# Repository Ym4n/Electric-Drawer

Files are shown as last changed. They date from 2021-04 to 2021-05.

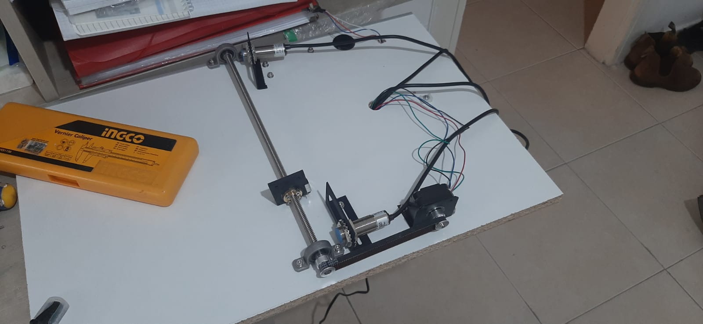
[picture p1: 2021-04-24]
pic & video/Assembly.jpeg

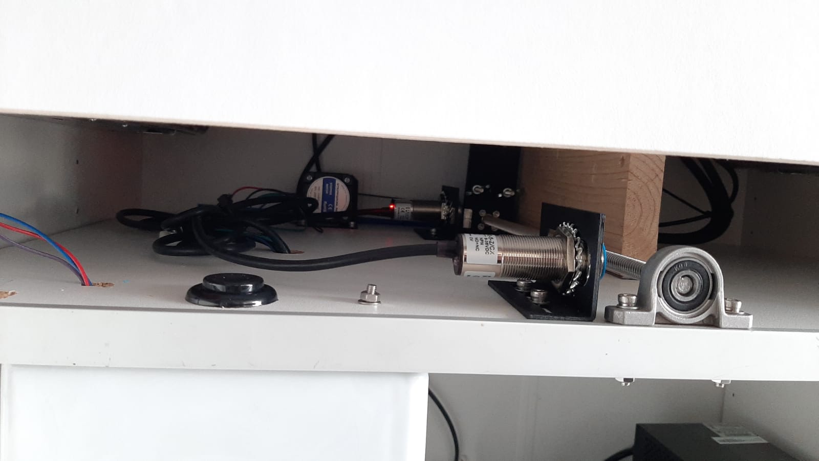
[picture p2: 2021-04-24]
pic & video/Final result.jpeg

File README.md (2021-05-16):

# Electric-Drawer
Electric Drawer for laser projector. control by Arduino.

https://user-images.githubusercontent.com/82320340/115971307-6bd4b180-a550-11eb-89f3-70404eacda08.mp4

# The Goal -
1.  Drawer can pool in and out to a specific position - No more manual operation.
2. Accuracy position - No more fine tune the projector to the accurate projection position. 
With every 1mm of distance between projector’s back to the projection surface, 0.2 inches are gained in picture size. 
see video below -

https://user-images.githubusercontent.com/82320340/115971346-9a528c80-a550-11eb-801a-cefcc77d8984.mp4

# How Dose it work?
1. User sends command with a remote control to IR reader or click on an arcade button . 
(Note: currently I aded 2 remotes. You can add/remove/change it)
2. IR-reader/button signal connected to Arduino.
3. Arduino decides to which position to get to. Far out or far in. 
In case of the drawer is already in the correct position, no movement will be made. 
(This is being determined by the Arduino using the two sensors that are located at the beginning and end of the movement range).
4. Motion control by arduino ,stepper motor and inductive sensors.

you can check mechanical design at solidworks folder or electrical design in electrical drawing .

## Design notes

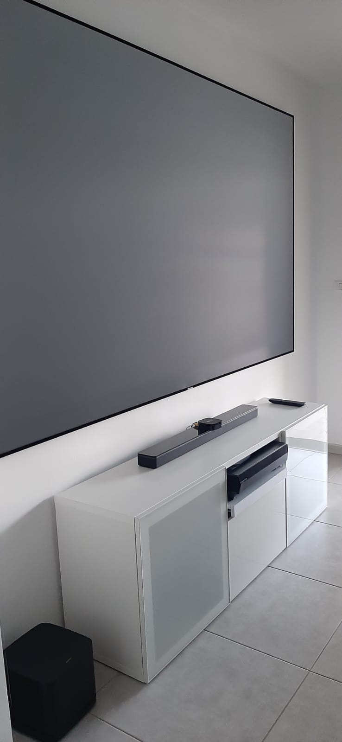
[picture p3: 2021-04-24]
pic & video/top view.jpeg

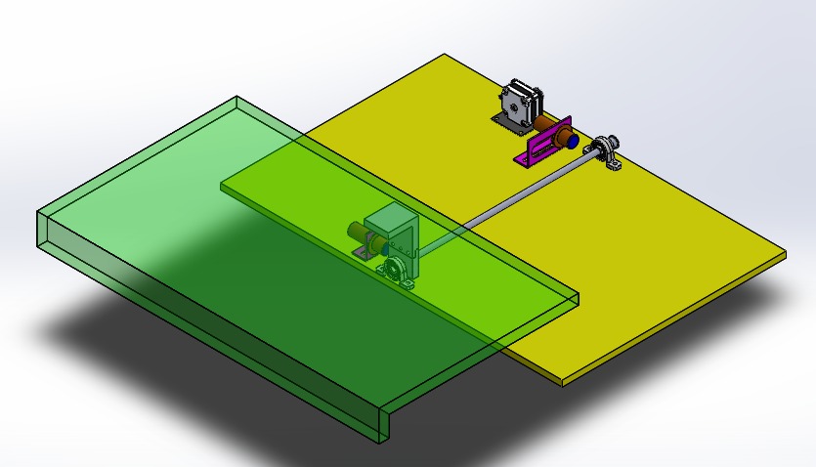
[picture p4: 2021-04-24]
pic & video/Solidworks.jpeg

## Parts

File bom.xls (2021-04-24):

ITEM NO. | PART NAME | QTY. | supplier
1 | bearing KP08 | 2 | Aliexpress
2 | lead screw Lead-8mm Len-350mm | 1 | Aliexpress
3 | Short Body Nema 17 17HS08-1004S | 1 | Aliexpress
4 | Inductive sensor | 2 | Aliexpress
5 | Pulley 8mm | 1 | Aliexpress
6 | Pulley 5mm | 1 | Aliexpress
7 | T8 nut | 1 | Aliexpress
8 | Arcade Button | 1 | Aliexpress
9 | Terminal block | 1 | Aliexpress
10 | electronics box 150x190 | 1 | Electronic store
11 | Arduino uno | 1 | Electronic store
12 | l298n motor driver | 1 | Electronic store
13 | Infra red remote control kit | 1 | Electronic store
14 | power supply 12v 2A | 1 | Electronic store
15 | Mount Inductive sensor | 2 | 3D printing
16 | MotorMount_NEMA | 1 | 3D printing
17 | finger down | 1 | 3D printing
18 | finger up | 1 | 3D printing
19 | plate | 1 | Recycled wood
20 | drawer | 1 | Recycled wood
21 | cabinet base | 1 | -

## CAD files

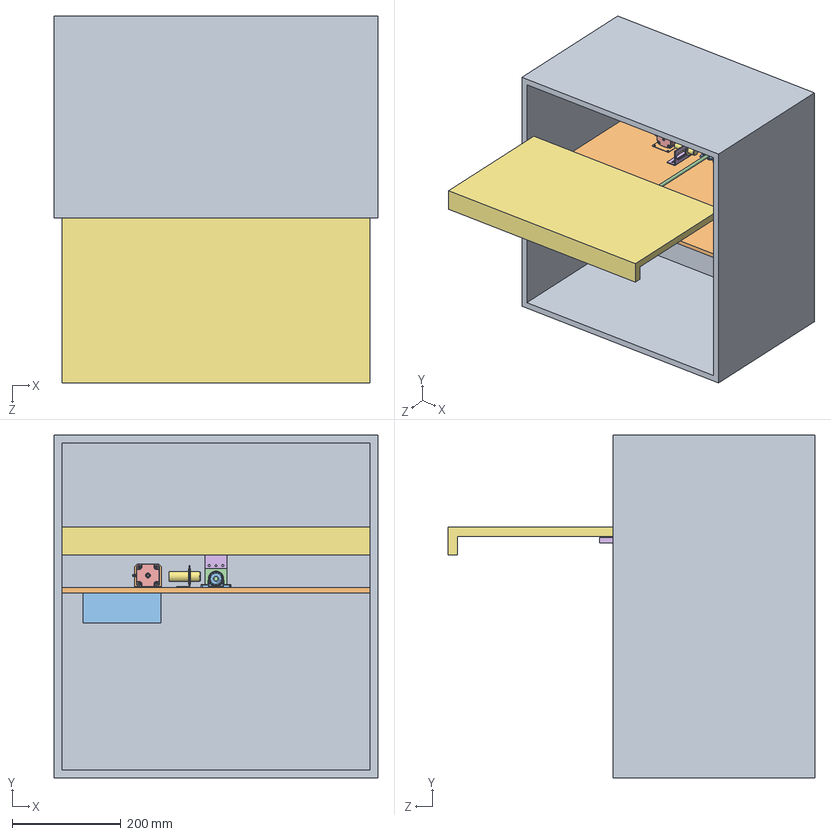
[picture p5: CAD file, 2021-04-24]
solidworks/main.SLDASM
595.0 x 630.0 x 674.0 mm
plate
bearing KP08 x 2
lead screw Lead-8mm Len-350mm
17HS08-1004S
slot Inductive sensor x 2
Inductive sensor x 2
Pulley 8mm
Pulley 5mm
MotorMount_NEMA
electronics box 150x190
finger down
T8 nut
finger up
drawer

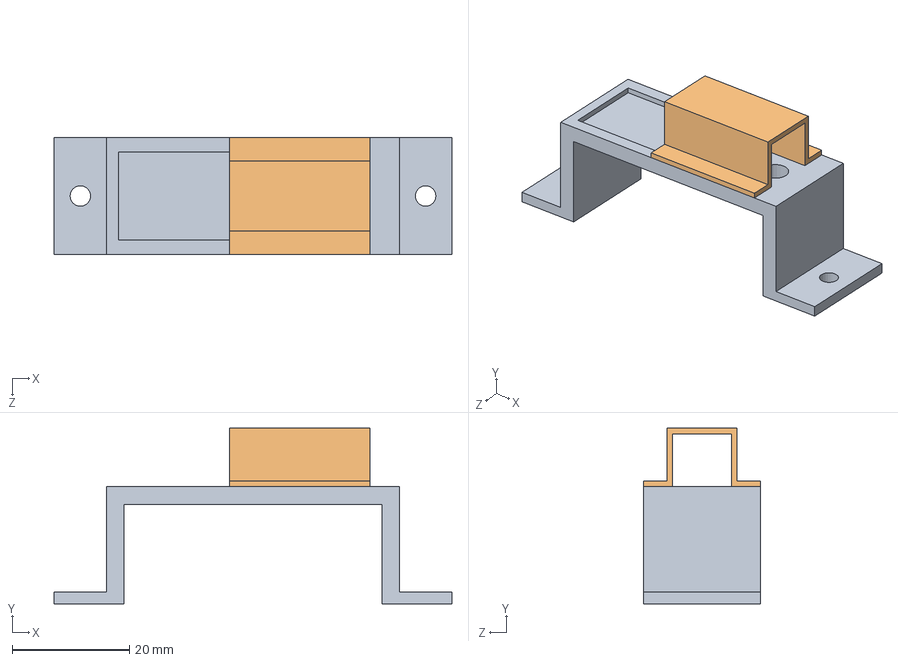
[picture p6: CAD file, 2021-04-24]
solidworks/remote base.SLDASM
68.0 x 30.0 x 20.0 mm
remote sensor house
remote sensor house2

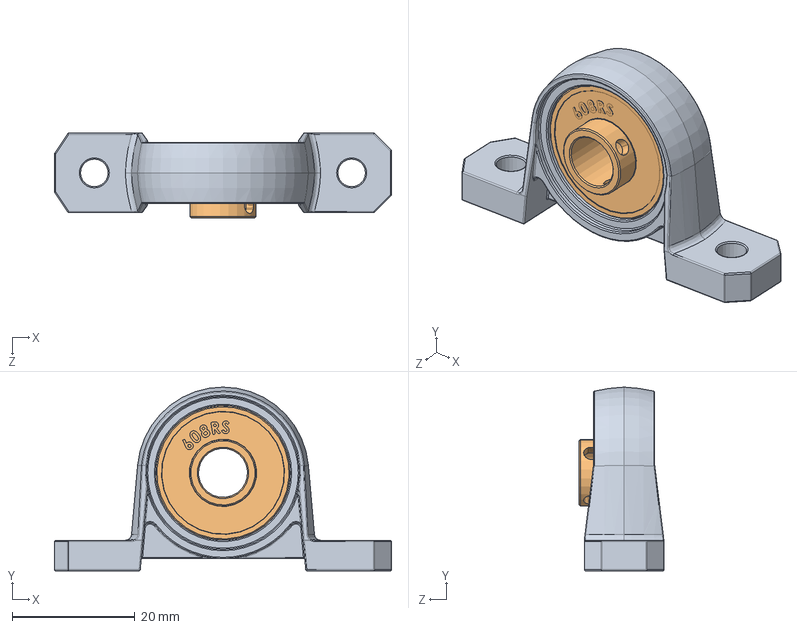
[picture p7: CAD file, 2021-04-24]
solidworks/KP08.SLDASM
55.0 x 30.0 x 13.9 mm
KP08
608RS

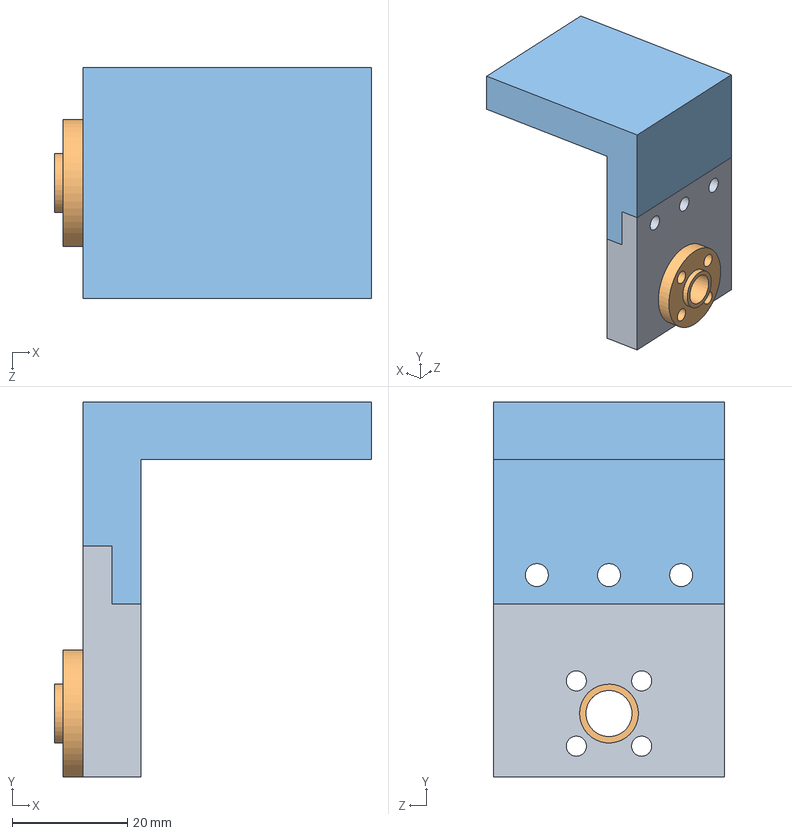
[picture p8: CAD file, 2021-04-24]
solidworks/moving part.SLDASM
55.0 x 65.0 x 40.0 mm
finger down
T8 nut
finger up

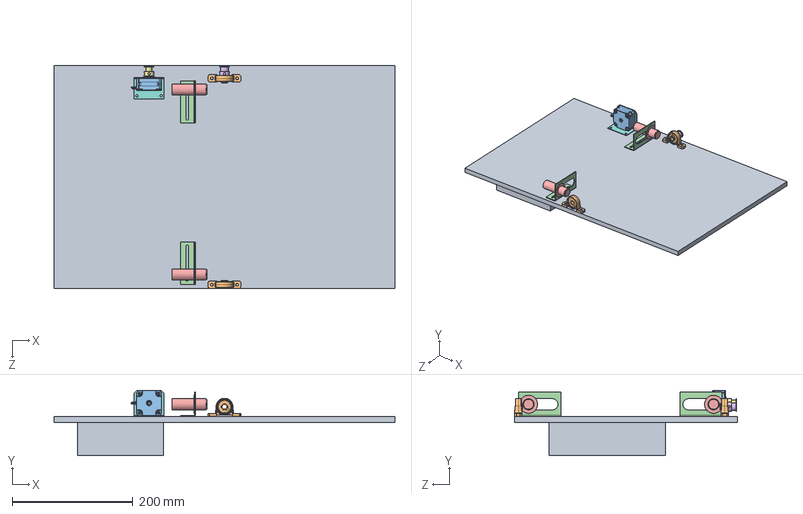
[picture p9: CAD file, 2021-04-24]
solidworks/sum-main motion control assembly.SLDASM
565.0 x 108.0 x 370.0 mm
plate
bearing KP08 x 2
17HS08-1004S
slot Inductive sensor x 2
Inductive sensor x 2
Pulley 8mm
Pulley 5mm
MotorMount_NEMA
electronics box 150x190

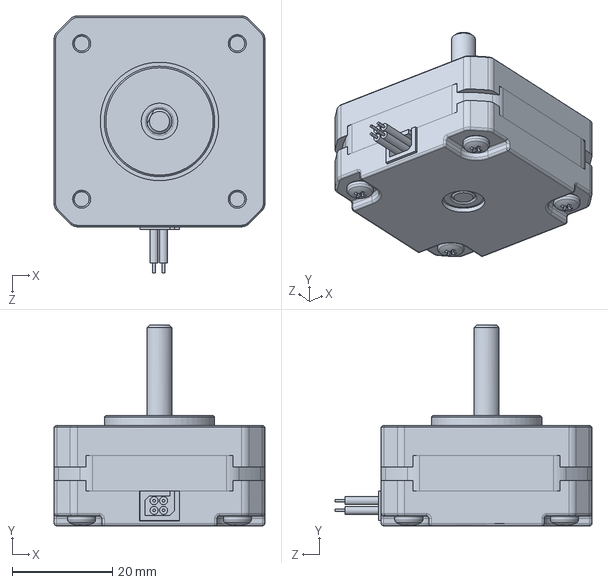
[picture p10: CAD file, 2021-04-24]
solidworks/Short Body Nema 17 17HS08-1004S.SLDPRT
42.0 x 40.0 x 51.2 mm

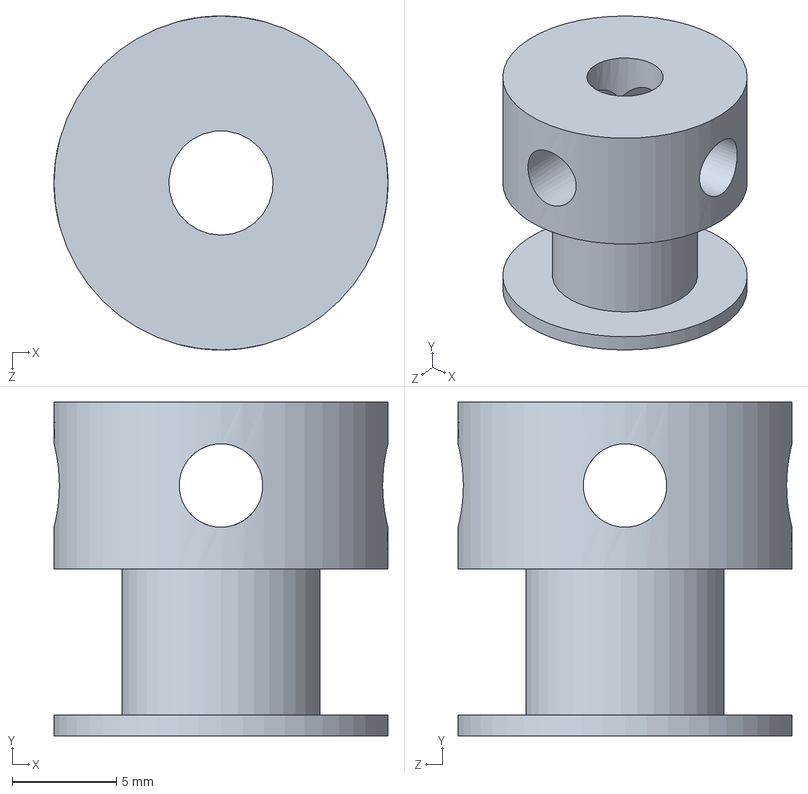
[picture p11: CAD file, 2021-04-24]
solidworks/Pulley 5mm.SLDPRT
16.0 x 16.0 x 16.0 mm

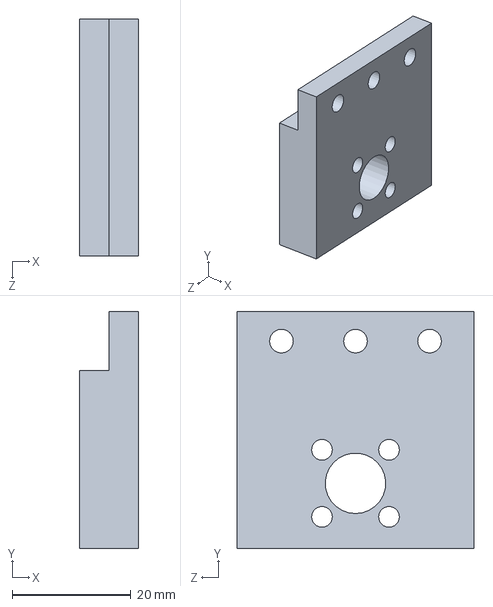
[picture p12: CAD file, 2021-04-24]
solidworks/finger down.SLDPRT
10.0 x 40.0 x 40.0 mm

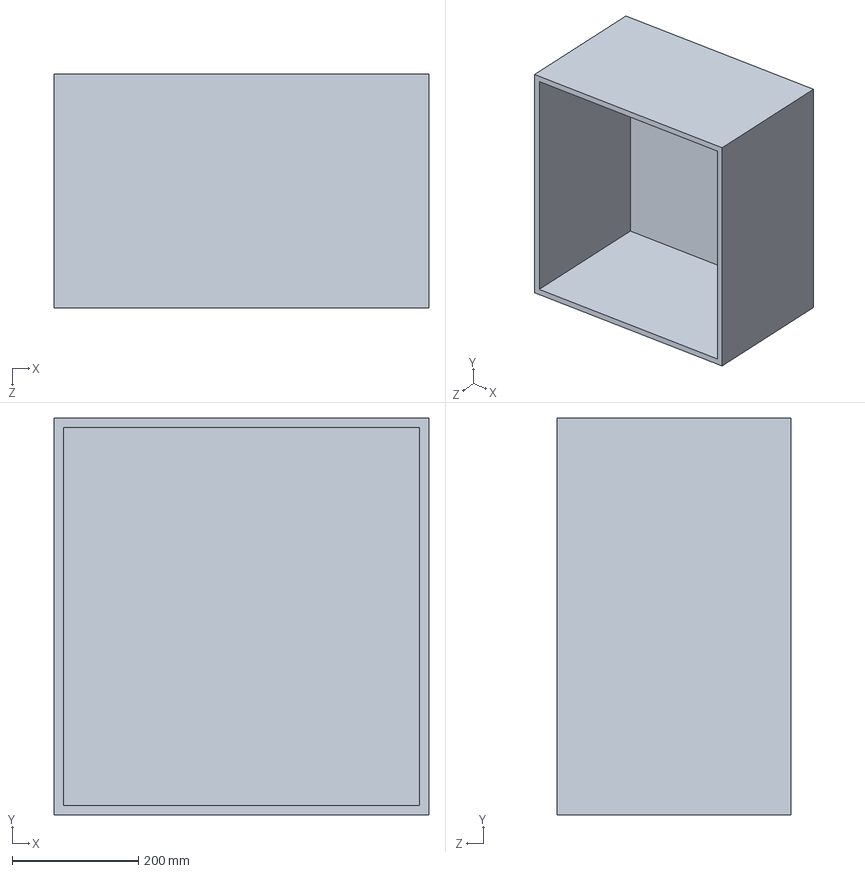
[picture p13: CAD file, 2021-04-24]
solidworks/cabinet base.SLDPRT
595.0 x 630.0 x 371.0 mm

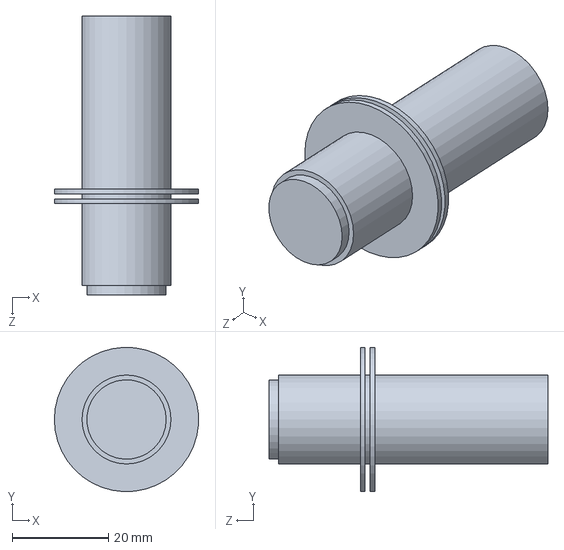
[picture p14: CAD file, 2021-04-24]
solidworks/Inductive sensor.SLDPRT
30.0 x 30.0 x 58.0 mm

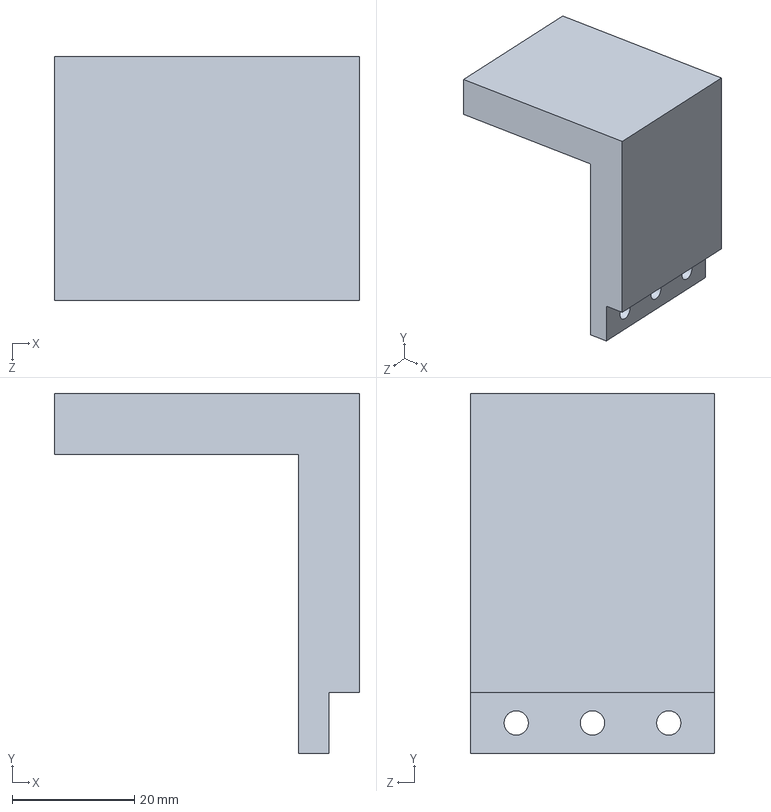
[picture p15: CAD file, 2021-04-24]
solidworks/finger up.SLDPRT
50.0 x 59.0 x 40.0 mm

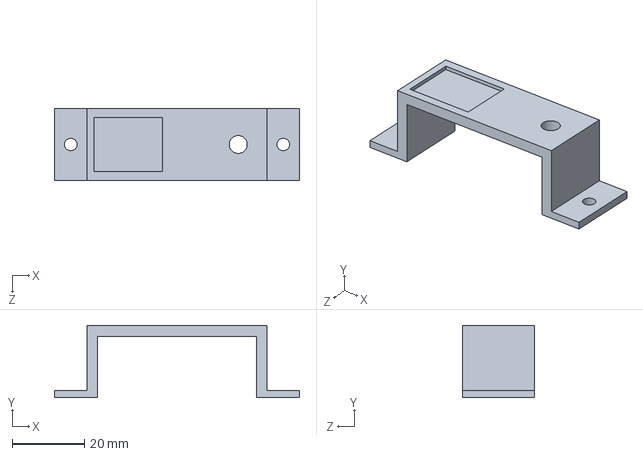
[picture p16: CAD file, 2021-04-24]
solidworks/remote sensor house.SLDPRT
68.0 x 20.0 x 20.0 mm

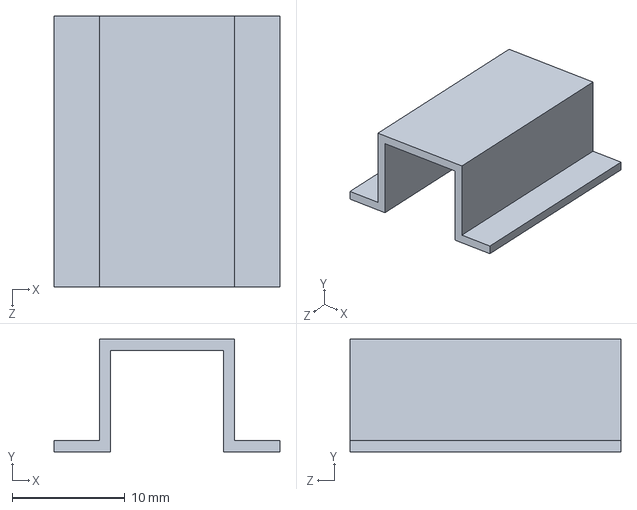
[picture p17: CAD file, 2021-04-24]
solidworks/remote sensor house2.SLDPRT
20.0 x 10.0 x 24.0 mm

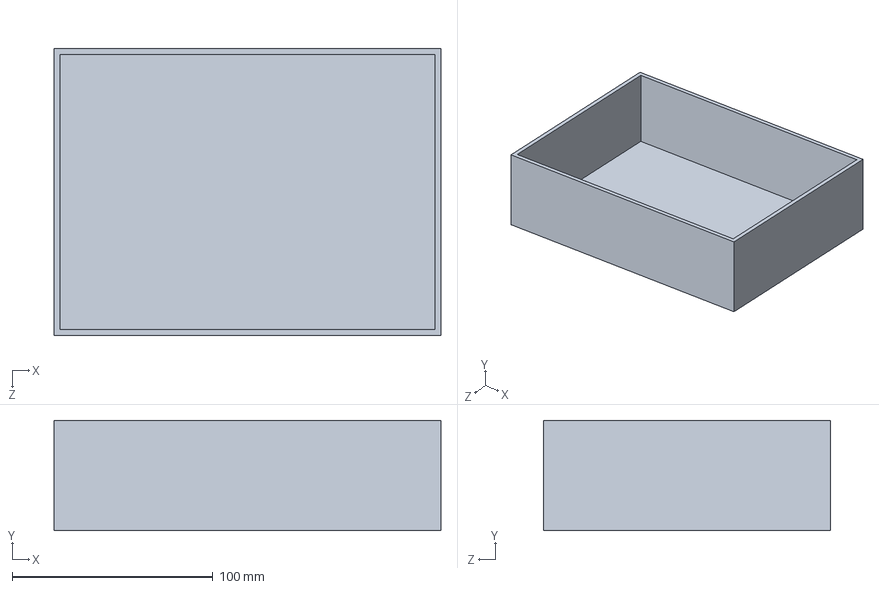
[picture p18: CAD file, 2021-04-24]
solidworks/electronics box 150x190.SLDPRT
193.0 x 55.0 x 143.0 mm

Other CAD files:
solidworks/bearing KP08.SLDPRT
solidworks/Pulley 8mm.SLDPRT
solidworks/plate.SLDPRT
solidworks/MotorMount_NEMA.SLDPRT
solidworks/Mount Inductive sensor.SLDPRT
solidworks/T8 nut.SLDPRT
solidworks/drawer.SLDPRT
solidworks/lead screw Lead-8mm Len-350mm.SLDPRT
solidworks/t8_nut_housing.SLDPRT

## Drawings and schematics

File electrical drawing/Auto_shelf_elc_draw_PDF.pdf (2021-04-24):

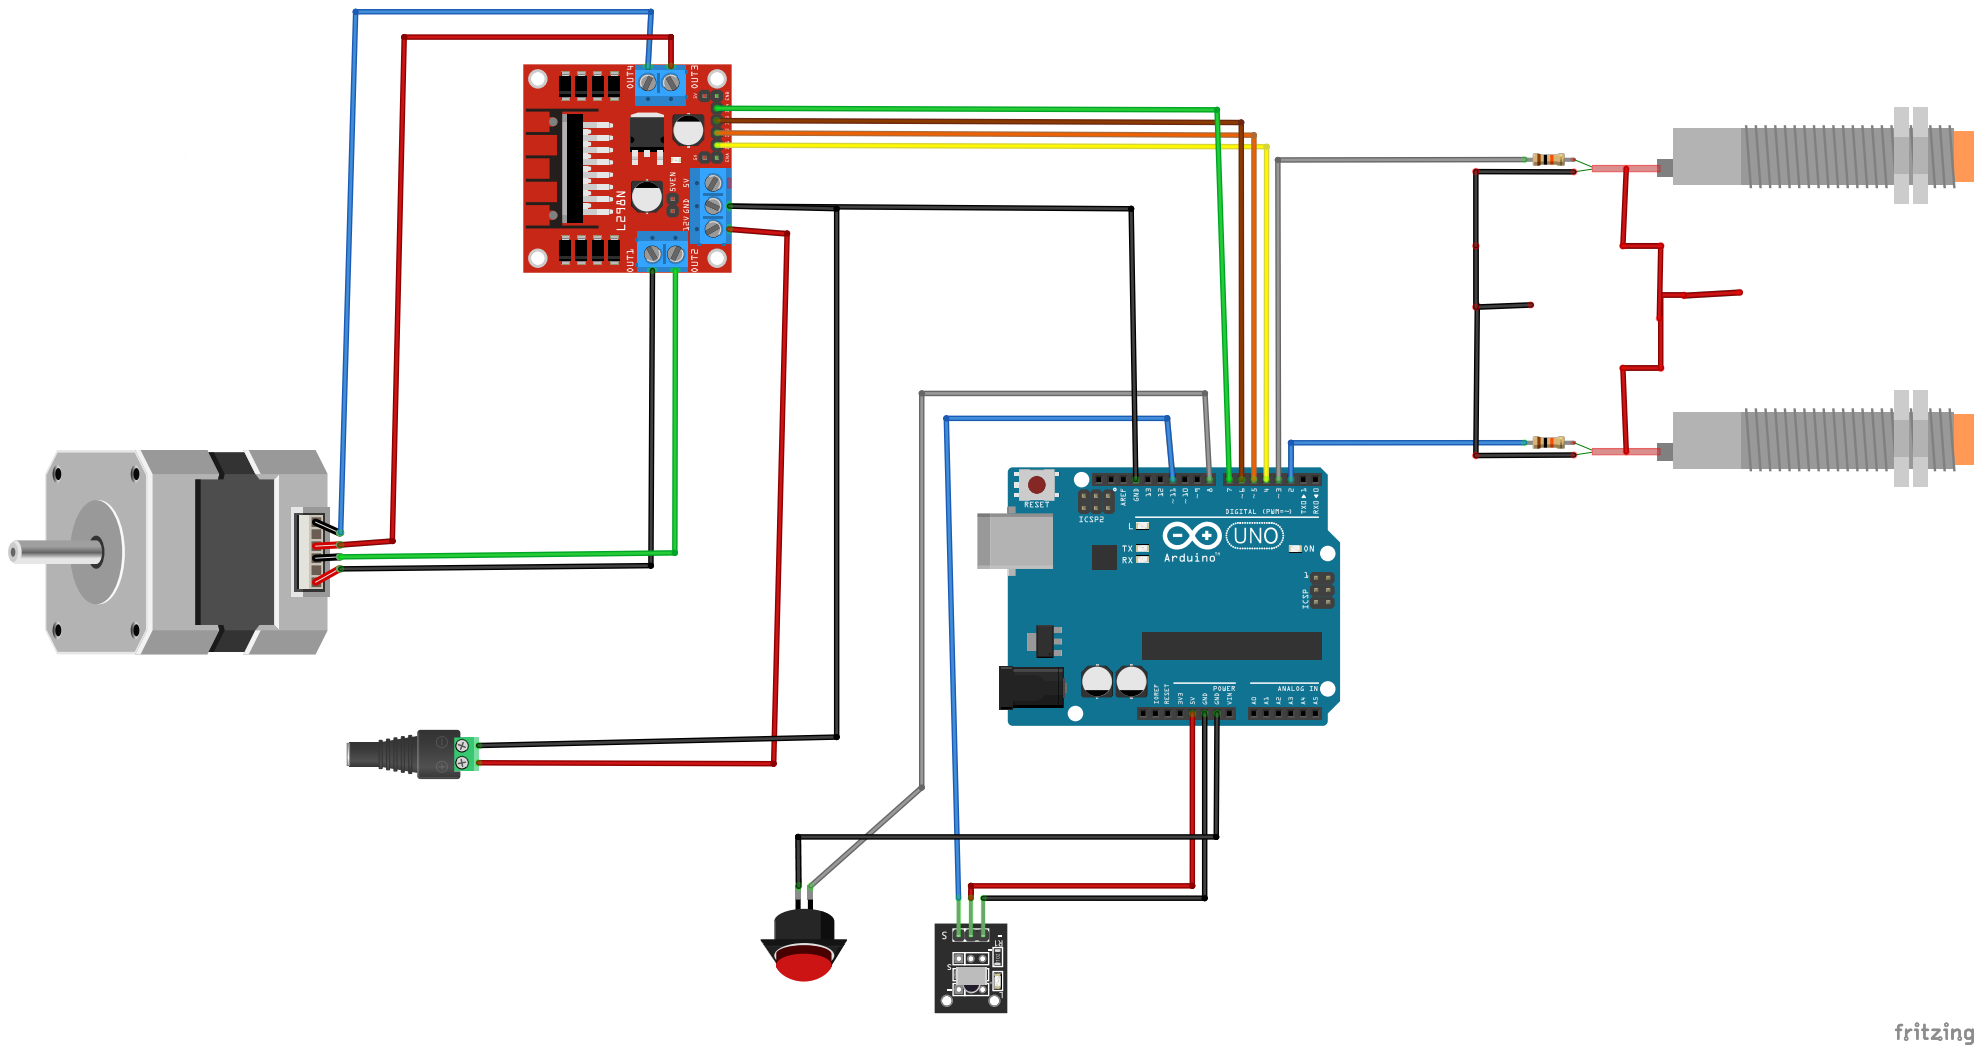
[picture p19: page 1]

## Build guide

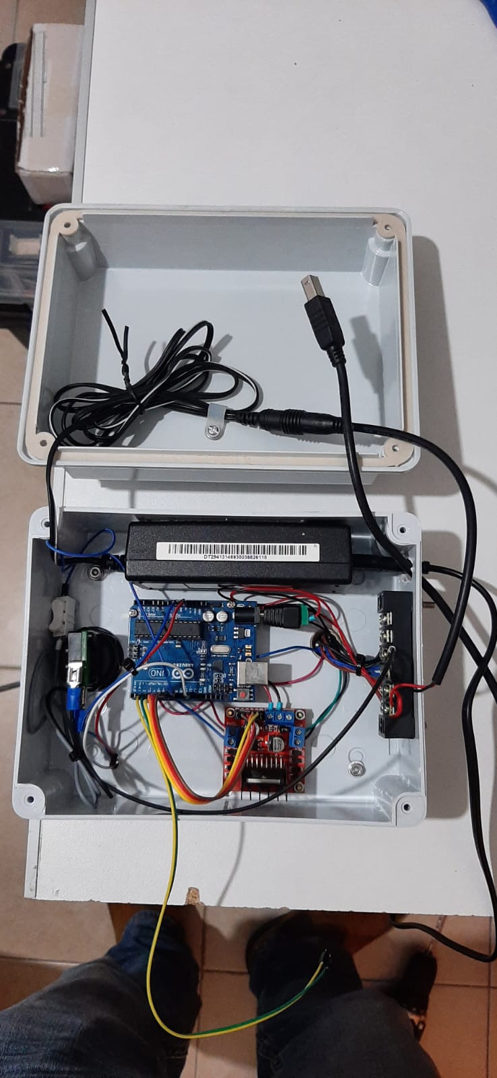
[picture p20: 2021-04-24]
pic & video/Wiring.jpeg

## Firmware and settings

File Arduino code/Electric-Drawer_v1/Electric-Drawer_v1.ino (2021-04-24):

#include <Stepper.h>


#include <IRremote.h>


// 150 is the max speed we can get
#define MotorSpeed 150  // 150 
#define stepsPerRevolution 200
#define Steps_for_1cm 250
#define buttonPin 8
#define Sensor_Home 2
#define Sensor_Far 3
#define DECODE_NEC 1
#define IR_RECEIVE_PIN  9
#define Sensor_Blocked false
#define Sensor_Open true


Stepper myStepper(stepsPerRevolution, 4, 5, 6, 7);

bool Dirction_back = false;
// the movement of the jig ( 200steps==1rev==0.8cm , 1cm==250steps)
int Jig_increment = Steps_for_1cm/10;

int Current_Location = 0;
int Target_Location = 0;
// steps between Start to End of the movement 
int Edge_to_Edge_steps = Steps_for_1cm*27; // need to be - 28

bool available_for_new_mission = true;

// Repeat_flag - for jig movement run smootly . 
// 1 ==> JIG move Back, 2 ==> JIG move Forward, 0 ==> Not JIG
int Repeat_flag = 0 ;

// JIG - moving by XX cm  
void JIG_MOVE(){
  if (Dirction_back==true){
    if (digitalRead(Sensor_Home)==Sensor_Open){
      Target_Location = Current_Location - Jig_increment;
    }
    else{
      Target_Location = Current_Location;
    }
  }
  else{
    if (digitalRead(Sensor_Far)==Sensor_Open){
      Target_Location = Current_Location + Jig_increment;
    }
    else{
      Target_Location = Current_Location;
    } 
  }
  move();
  //available_for_new_mission=false;
}

// Edge to Edge movement 
void Edge_move(){
  Serial.println("Edge move");
  if (digitalRead(Sensor_Home)==Sensor_Blocked){
    Current_Location=0;
  }

  if (Current_Location==0){
    Dirction_back=false;
    Target_Location = Edge_to_Edge_steps*-1;
  }
  else{
    Target_Location = 0;
    Dirction_back=true;
  }
  available_for_new_mission =false;
}

void Stop_motor(){
  digitalWrite(4,LOW);
  digitalWrite(5,LOW);
  digitalWrite(6,LOW);
  digitalWrite(7,LOW);
}


// increment movement
void move(){
  if (Current_Location==Target_Location){
    available_for_new_mission= true;
    Stop_motor();
  }
  int Steps = stepsPerRevolution/2;
  int gap = abs(Current_Location - Target_Location);
  Serial.print("Current Location and Target_Location : ");
  Serial.print(Current_Location);
  Serial.print("  ,  ");
  Serial.println(Target_Location);
  if (Steps > gap){
    Steps= gap;
  }
  if (Dirction_back){
    myStepper.step(Steps);
    Current_Location += Steps;
  }
  else{
    myStepper.step(-Steps);
    Current_Location -= Steps;
  }
}

void Sensor_Home_Reach(){
  Stop_motor();
  Dirction_back = !Dirction_back;
  available_for_new_mission = true;
  Current_Location=0;
  Serial.println("Reach to the Home Pos");
}

void Sensor_Far_Reach(){
  Stop_motor();
  Dirction_back = !Dirction_back;
  Serial.println("Reach to the End");
  available_for_new_mission = true;
}

// Remote functions
void read_Remote(){
  if (IrReceiver.decode()) {
        // Chaines Remote
        if (IrReceiver.decodedIRData.address==0){
          if (available_for_new_mission==true){
            switch(IrReceiver.decodedIRData.decodedRawData) {
            case 0xE718FF00:                      // UP arrow - Move to Home Pos
              Serial.println("go back");
              Dirction_back=true; 
              Repeat_flag = 1 ;
              JIG_MOVE();
              break;   
            
            case 0xAD52FF00:                      // down arrow - Move Out
              Serial.println("go forward");
              Dirction_back=false; 
              Repeat_flag = 2 ;
              JIG_MOVE(); 
              break;   
            
            case 0xE31CFF00:                      // OK btn
              Serial.println(" -OK- Stop motors"); 
              Repeat_flag = 0 ;
              Stop_motor();
              break;             
            
            case 0xB946FF00:                      // 2 - move to home pos
              Repeat_flag = 0 ;
              if (digitalRead(Sensor_Home)!=Sensor_Blocked){
                Current_Location =Edge_to_Edge_steps ;
                Edge_move();
              }
              break;                              
            
            case 0xEA15FF00:                      // 8 - move to far pos
              Repeat_flag = 0 ; 
              if (digitalRead(Sensor_Far)!=Sensor_Blocked){
                Current_Location = 0 ;
                Edge_move();
              }
              break;                
            
            case 0x0: 
              switch (Repeat_flag)
              {
              case 1:
                Dirction_back=true; 
                JIG_MOVE();
                break;
              
              case 2:
                Dirction_back=false; 
                JIG_MOVE();
                break;
              }
              break;
            
            default:
              Repeat_flag = 0 ;
            }
            delay(200); // Do not get immediate repeat
          }
          else{
            if (IrReceiver.decodedIRData.decodedRawData==0xE31CFF00){
              Stop_motor();
              available_for_new_mission=true;
              delay(200);
            }
          }
        }
        // Polaris Remote
        if (IrReceiver.decodedIRData.address==0xCF00){
          if (available_for_new_mission==true){
            switch(IrReceiver.decodedIRData.command) {
              case 0xB:                                    // - btn
                Serial.println("Feldman remote");
                Serial.println(" - btn");
                Repeat_flag = 0 ;
                if (digitalRead(Sensor_Home)!=Sensor_Blocked){
                  Current_Location =Edge_to_Edge_steps ;
                  Edge_move();
                }
                break;

              case 0xA:                                    // + btn
                Serial.intln("Feldman remote");
                Serial.priprntln(" + btn");
                Repeat_flag = 0 ; 
                if (digitalRead(Sensor_Far)!=Sensor_Blocked){
                  Current_Location = 0 ;
                  Edge_move();
                }
                break;
              
              case 0x1A:                                    // Power(ON/OFF) btn
                Serial.println("Feldman remote");
                Serial.println(" Power btn");
                Repeat_flag = 0 ;
                if (digitalRead(Sensor_Home)!=Sensor_Blocked){
                  Current_Location =Edge_to_Edge_steps ;
                  Edge_move();
                }
                break;
            }
          }


        }
        IrReceiver.resume(); // Enable receiving of the next value
    }
}

void setup()
{  
  pinMode(buttonPin, INPUT_PULLUP);
  pinMode(4, OUTPUT);
  pinMode(5, OUTPUT);
  pinMode(6, OUTPUT);
  pinMode(7, OUTPUT);
  pinMode(Sensor_Home, INPUT_PULLUP);
  pinMode(Sensor_Far, INPUT_PULLUP);
  attachInterrupt(digitalPinToInterrupt(Sensor_Home), Sensor_Home_Reach, FALLING);
  attachInterrupt(digitalPinToInterrupt(Sensor_Far), Sensor_Far_Reach, FALLING);
  IrReceiver.begin(IR_RECEIVE_PIN, ENABLE_LED_FEEDBACK, USE_DEFAULT_FEEDBACK_LED_PIN);

  if (digitalRead(Sensor_Far)==0){
    Current_Location = -Edge_to_Edge_steps;
  }
  Serial.println(Current_Location);
  myStepper.setSpeed(MotorSpeed);
  Serial.begin(9600);
  Serial.println("Setup Done");
  Serial.println(Current_Location);
}

void loop(){   
  if (available_for_new_mission){
    Stop_motor();
    //check buttom
    if (digitalRead(buttonPin)==false){
      // Edge_move
      Edge_move();
      Serial.println("Button clicked");
    }
    read_Remote();
  }
  else{
    read_Remote();
    move();
  }
}

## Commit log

2021-04-24 electrical drawing
    [Auto_shelf_elc_draw.fzz]
2021-04-24 bill of material
    [bom.xls]
2021-04-24 arduino code
2021-04-24 bill of materials
    [bom.xls]
